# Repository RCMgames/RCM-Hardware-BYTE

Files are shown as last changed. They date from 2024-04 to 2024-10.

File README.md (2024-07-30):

# RCM-Hardware-BYTE
v2.3

* 1.25 by 1.25 inches, 31.75 by 31.75 millimeters
* 8 motors
* 8 servos
* battery monitoring
* I2C connector on QT PY
* runs on 3-11 volts

### Tested with the following types of ESP32 QT Py:
| Type of Qt Py | PlatformIO name | link to Adafruit |
| --- | --- | --- |
| S3 with 2MB PSRAM |  adafruit_qtpy_esp32s3_n4r2 |  https://www.adafruit.com/product/5700 |
| S3 with 8Mb Flash |  adafruit_qtpy_esp32s3_nopsram |  https://www.adafruit.com/product/5426 |
| S2 |  adafruit_qtpy_esp32s2 |  https://www.adafruit.com/product/5325  |

Look here for how to program it: https://github.com/RCMgames/RCMv2

Look here for more information and examples of robots: https://github.com/rcmgames

Want slightly smaller with a built in IMU? Look at the [Nibble](https://github.com/RCMgames/RCM-Hardware-Nibble)

## Options for purchasing

* [PCBWay link](https://www.pcbway.com/project/shareproject/RCMHardwareByte_v2_3_e23eec63.html) (PCBWay will give me a commission without increasing the price for you). (approximately $90 for 2 boards and manufacturing took a month).
* send the gerbers, bill of materials, and ComponentPlacement files to a PCB manufacturer of your choice (details you may be asked for: min hole 0.25mm, min track/spacing 5/5mil, thickness 1.0mm, 1 oz Cu outer 1.5 oz Cu inner)

## Components
Solder by hand to complete the assembly of your boards.
| part | links | quantity | notes |
| ----- | ----- | ----- | ----- |
| RCM BYTE circuit board | [options for purchasing](https://github.com/RCMgames/RCM-Hardware-BYTE/tree/main#options-for-purchasing) | 1 | |
| ESP32 QT Py | [compatible QT Py](https://github.com/RCMgames/RCM-Hardware-BYTE/tree/main#tested-with-the-following-types-of-esp32-qt-py) | 1 | |
| 2x8 female header pins | [this](https://www.digikey.com/en/products/detail/sullins-connector-solutions/PPPC042LFBN-RC/810244) or 2 strips of 8 | 1 | for motors |
| 7 female header pins | | 2 | for QT Py |
| 8 male header pins | | 4 | for servos |
| battery wires | JST RCY OR 9V battery snap | 1 | [Amazon JST RCY](https://www.amazon.com/dp/B00Z04QFN2/) |
| servo buck boost 5v 2A OR replace with a short length of wire| [Pololu](https://www.pololu.com/product/4085) | 2 | regulators are needed if you want to supply voltages above or below what servos can accept. There are 2 servo power buses, each with 4 servos. |

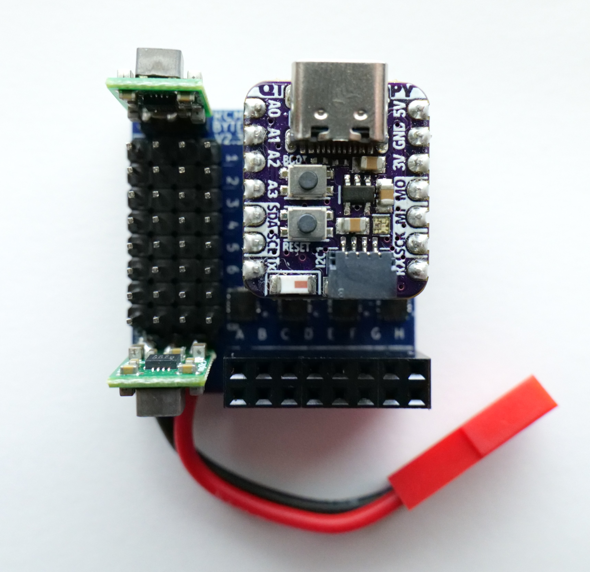
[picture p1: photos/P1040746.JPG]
front view

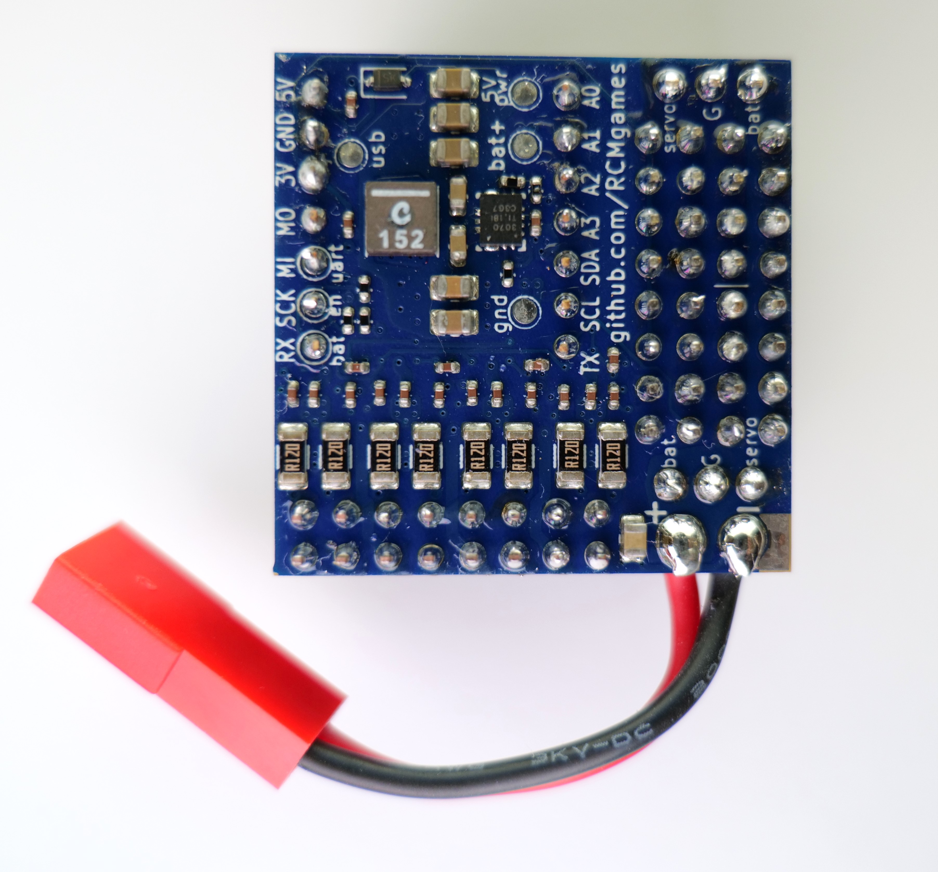
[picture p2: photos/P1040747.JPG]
back view


## Acknowledgements
* I would like to thank [PCBWay](https://www.pcbway.com/) for sponsoring prototyping runs of this project. PCBWay produces very nice boards, supports open source hardware, and gave me great support as I worked on this project. Special thanks to Liam!

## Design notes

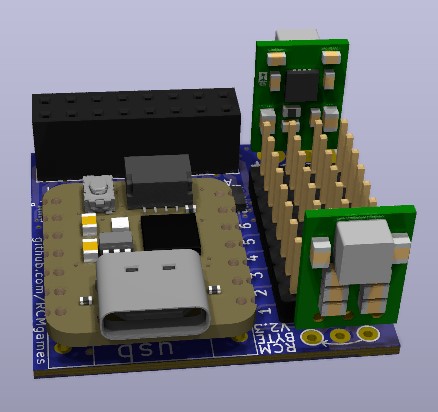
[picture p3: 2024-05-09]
CAD renders/render 1.jpg

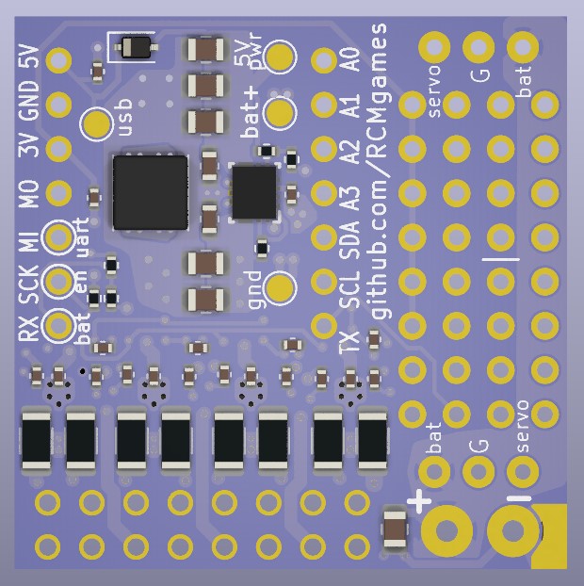
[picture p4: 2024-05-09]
CAD renders/back.jpg

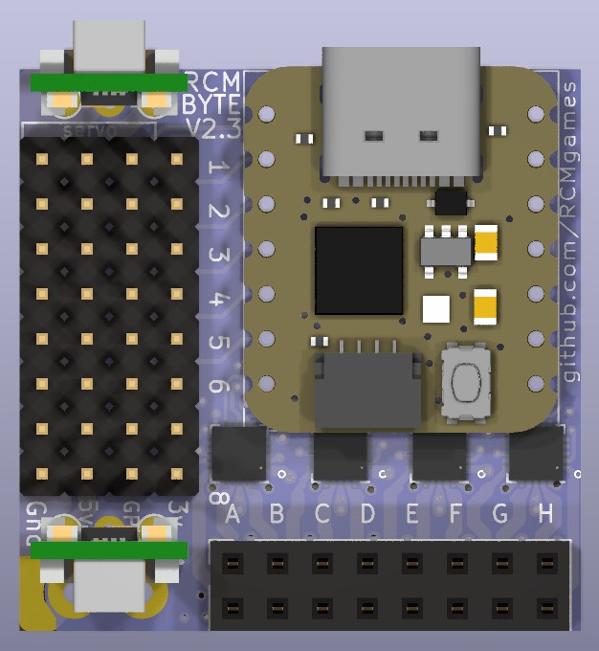
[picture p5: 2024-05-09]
CAD renders/top.jpg

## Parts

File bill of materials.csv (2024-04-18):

Reference | Value | Footprint | Datasheet | Manufacturer | Package | digikey part # | link | mount_type | mpn | Qty
C1, C3-C15, C17-C20, C22 | 100nF/0402/16V/X7R/<=10%/ceramic | Capacitor_SMD:C_0402_1005Metric | ~ | Cal-Chip Electronics, Inc. | 0402 | 4713-GMC04X7R104K50NTCT-ND | https://www.digikey.com/en/products/detail/cal-chip-electronics-inc/GMC04X7R104K50NT/18151122 | smt | GMC04X7R104K50NT | 19
C2, C25-C27 | 22uF/0805/>=16V | Capacitor_SMD:C_0805_2012Metric | ~ | Cal-Chip Electronics, Inc. | 0805 | 4713-GMC21X5R226M16NTCT-ND | https://www.digikey.com/en/products/detail/cal-chip-electronics-inc/GMC21X5R226M16NT/19910713 | smt | GMC21X5R226M16NT | 4
C16, C21 | 10uF/0805/>=16V | Capacitor_SMD:C_0805_2012Metric | ~ | Cal-Chip Electronics, Inc. | 0805 | 4713-GMC21X7R106K16NTCT-ND | https://www.digikey.com/en/products/detail/cal-chip-electronics-inc/GMC21X7R106K16NT/18151068 | smt | GMC21X7R106K16NT | 2
C23, C24 | 10uF/0603/>=16V | Capacitor_SMD:C_0603_1608Metric | ~ | Cal-Chip Electronics, Inc. | 0603 | 4713-GMC10X5R106M25NTCT-ND | https://www.digikey.com/en/products/detail/cal-chip-electronics-inc/GMC10X5R106M25NT/18151144 | smt | GMC10X5R106M25NT | 2
D1 | 1A Zener Diode / >=1A / 600 mV Vf @ 1 A | Diode_SMD:D_SOD-323 | ~ | Good-Ark Semiconductor | D_SOD-323 | 4786-GDB5818WSCT-ND | https://www.digikey.com/en/products/detail/good-ark-semiconductor/GDB5818WS/18648294 | smt | GDB5818WS | 1
ESP32_QT_PY1 | microcontroller | !RCMhardware footprints:ESP32 QT PY | ~ | Adafruit | tht |  | https://www.digikey.com/en/products/detail/adafruit-industries-llc/5426/21283802 | do not place or purchase for PCB assembly |  | 1
IC1-IC4 | TMC7300 | !RCMhardware footprints:QFN-20-1EP_3x3mm_P0.4mm_EP1.65x1.65mm | https://www.analog.com/media/en/technical-documentation/data-sheets/TMC7300_datasheet_rev1.08.pdf | Analog Devices | QFN-20-1EP_3x3mm_P0.4mm_EP1.65x1.65mm | 175-TMC7300-LA-TCT-ND | https://www.digikey.com/en/products/detail/analog-devices-inc-maxim-integrated/TMC7300-LA-T/11483537 | smt | TMC7300-LA-T | 4
J1 | pads to solder wires to, recommend JST RCY | !RCMhardware footprints:battery wires | ~ |  | tht |  | https://www.amazon.com/dp/B00Z04QFN2/ | do not place or purchase for PCB assembly |  | 1
J2-J5 | 1x08 male header pins | !RCMhardware footprints:servo pin column | ~ |  | tht |  | https://www.digikey.com/en/products/detail/te-connectivity-passive-product/CRG0402F30K/2390530 | do not place or purchase for PCB assembly |  | 4
J6 | 2x08 female header pins | !RCMhardware footprints:PinSocket_2x08_P2.54mm_Vertical | ~ |  | tht |  | https://www.digikey.com/en/products/detail/sullins-connector-solutions/PPTC082LFBN-RC/810214 | do not place or purchase for PCB assembly |  | 1
L1 | XFL4020-1.5μH | !RCMhardware footprints:L_Coilcraft_XxL4020 | ~ | Coilcraft | 1616 | 2457-XFL4020-152MEC-ND | https://www.digikey.com/en/products/detail/coilcraft/XFL4020-152MEC/21381168 | smt | XFL4020-152MEC | 1
R1, R14 | 30k / <=1% | Resistor_SMD:R_0402_1005Metric | ~ | TE Connectivity Passive Product | 0402 | 1712-CRG0402F30KCT-ND | https://www.digikey.com/en/products/detail/te-connectivity-passive-product/CRG0402F30K/2390530 | smt | CRG0402F30K | 2
R2, R11, R12 | 10k / <=1% | Resistor_SMD:R_0402_1005Metric | ~ | TE Connectivity Passive Product | 0402 | A121528CT-ND | https://www.digikey.com/en/products/detail/te-connectivity-passive-product/CRG0402F10K/5246515 | smt | CRG0402F10K | 3
R3-R10 | 120mΩ / 0.5W / 1206 / <=1% | Resistor_SMD:R_1206_3216Metric | ~ | Bourns Inc. | 1206 | CRL1206-FW-R120ELFCT-ND | https://www.digikey.com/en/products/detail/bourns-inc/CRL1206-FW-R150ELF/3785721 | smt | CRL1206-FW-R120ELF | 8
R13 | 130k | Resistor_SMD:R_0402_1005Metric | ~ | TE Connectivity Passive Product | 0402 | A119923CT-ND | https://www.digikey.com/en/products/detail/te-connectivity-passive-product/CPF0402B130KE/4966473 | smt | CPF0402B130KE | 1
TP1-TP4 | TestPoint | TestPoint:TestPoint_Pad_D1.5mm | ~ | n/a | n/a | n/a | n/a | do not place or purchase for PCB assembly | n/a | 4
U1 | TPS63070 5V 2A buck-boost | !RCMhardware footprints:TPS630701RNMR | https://www.ti.com/lit/ds/symlink/tps63070.pdf | Texas Instruments | 15-VQFN-HR (3x2.5) | 296-44874-1-ND | https://www.digikey.com/en/products/detail/texas-instruments/TPS63070RNMR/6175216 | smt | TPS63070RNMR | 1
U5, U6 | 5V, 2A, buck boost | !RCMhardware footprints:pololu4085 | ~ | Pololu | tht |  | https://www.pololu.com/product/4085 | do not place or purchase for PCB assembly |  | 2

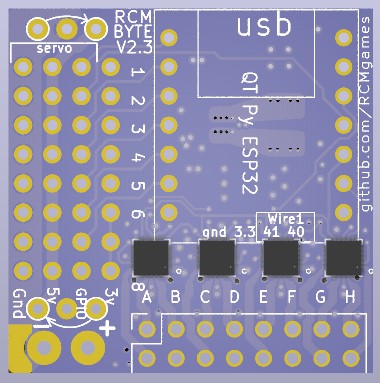
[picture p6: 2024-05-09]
CAD renders/top no components.jpg

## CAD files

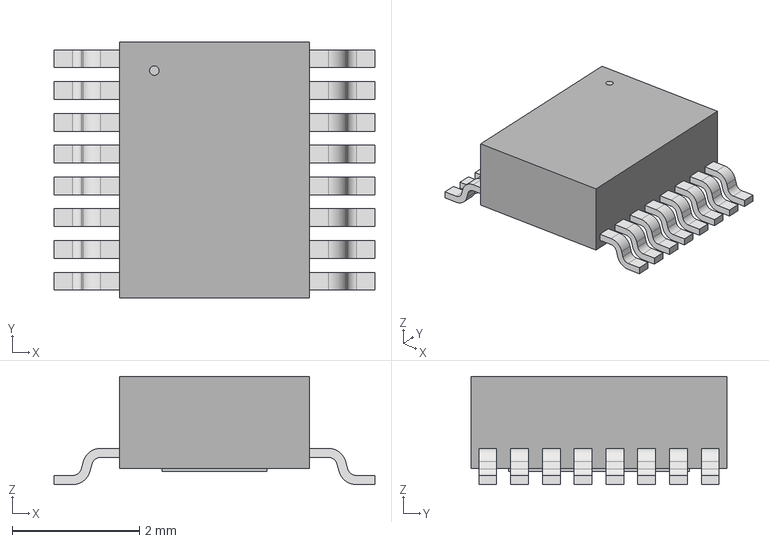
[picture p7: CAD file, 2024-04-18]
KiCad/!RCMhardware footprints/MSE_16_ADI.step
5.05 x 4.04 x 1.70 mm

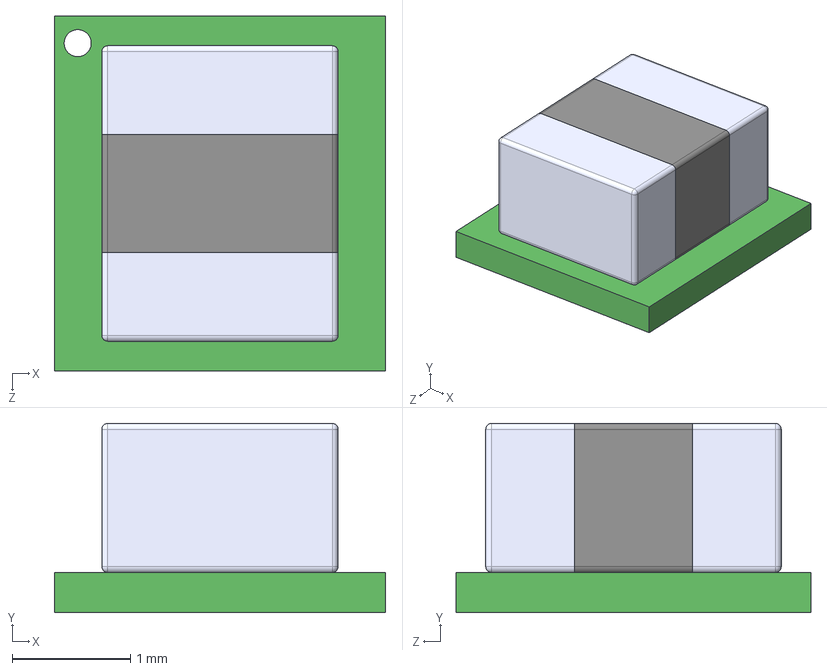
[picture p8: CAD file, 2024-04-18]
KiCad/!RCMhardware footprints/TPSM82903SISR--3DModel-STEP-56544.STEP
2.80 x 1.60 x 3.00 mm

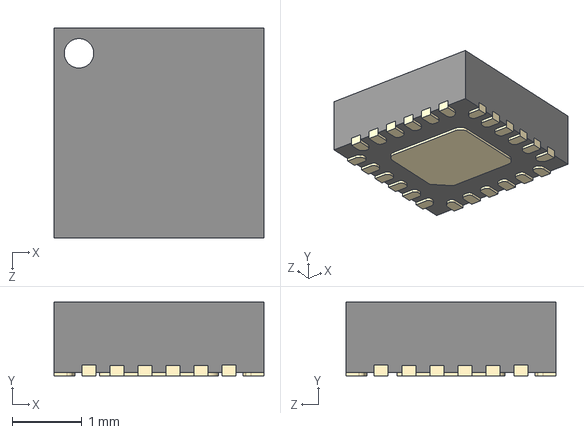
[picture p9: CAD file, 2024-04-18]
KiCad/!RCMhardware footprints/ICM-20948.step
3.00 x 1.05 x 3.00 mm

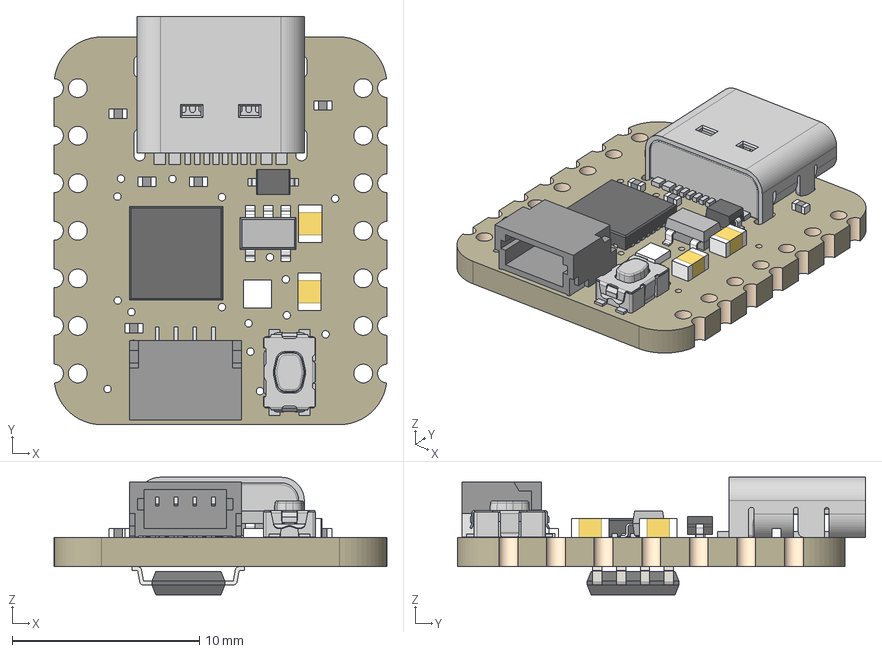
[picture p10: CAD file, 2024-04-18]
KiCad/!RCMhardware footprints/4600 QTPy.step
17.8 x 21.8 x 6.28 mm
Board
10uF x 2
reset
ATSAMD21E
TPB1,27
5.1K x 5
USB TYPE C
STEMMA_I2C_QTSKINNY
AP2112K-3.3
WS2812B_SK6805_1515
NSR0320
SOIC8_150MIL

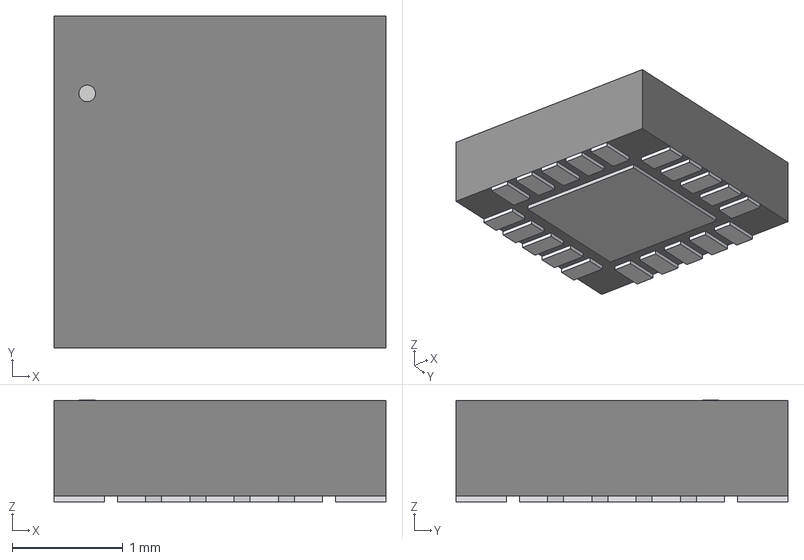
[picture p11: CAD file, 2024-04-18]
KiCad/!RCMhardware footprints/QFN20_3x3_TRI.step
3.00 x 3.00 x 0.917 mm

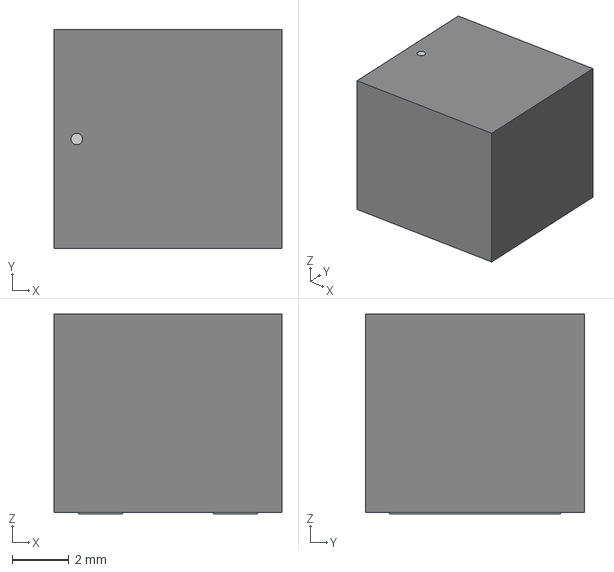
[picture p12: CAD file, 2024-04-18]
KiCad/!RCMhardware footprints/IND_XAL7070_COC.step
8.00 x 7.70 x 7.01 mm

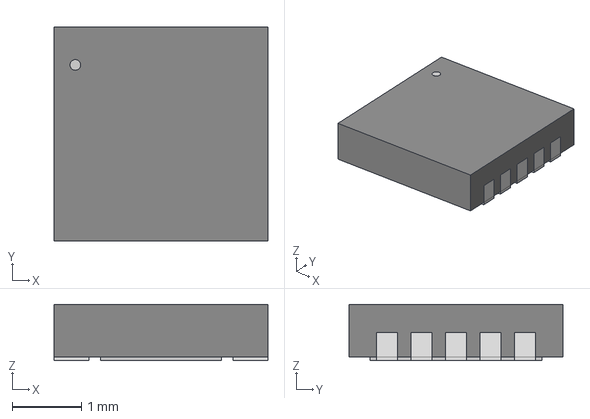
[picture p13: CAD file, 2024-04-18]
KiCad/!RCMhardware footprints/DFN-10_DD_LIT.step
3.10 x 3.10 x 0.815 mm

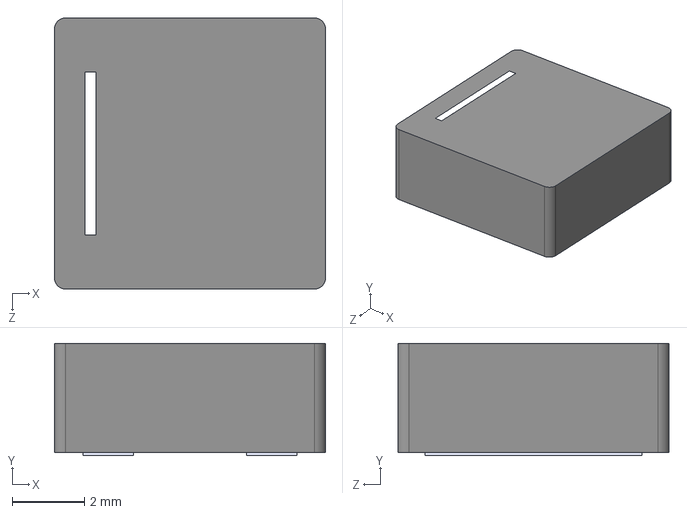
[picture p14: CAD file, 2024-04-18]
KiCad/!RCMhardware footprints/XAL7030-472MEC.step
7.50 x 3.10 x 7.50 mm

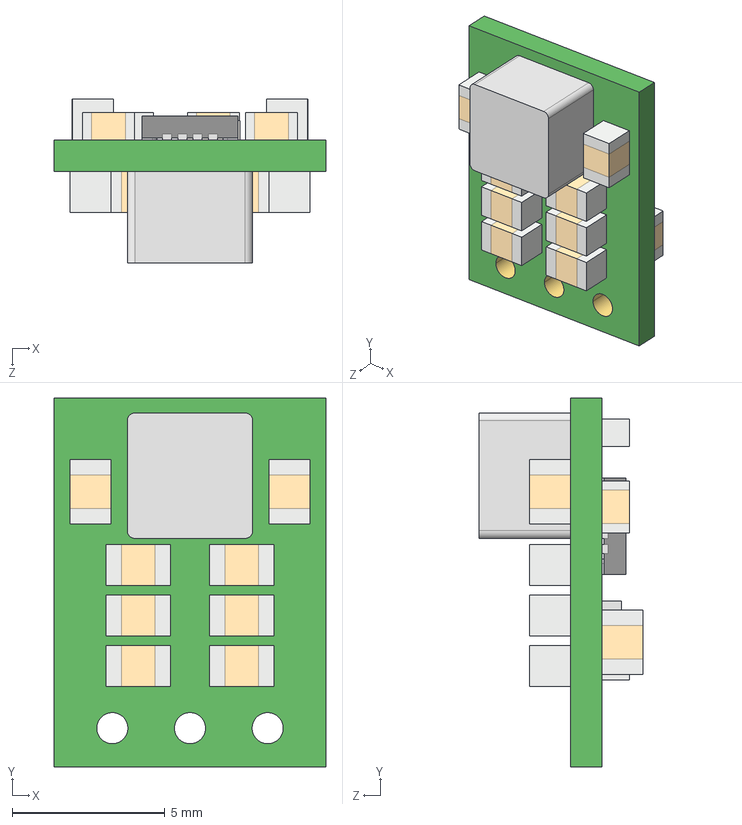
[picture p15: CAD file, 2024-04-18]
KiCad/!RCMhardware footprints/pololu 4085 5v-2a-step-up-step-down-voltage-regulator-s13v20f5.step
8.89 x 12.1 x 5.37 mm

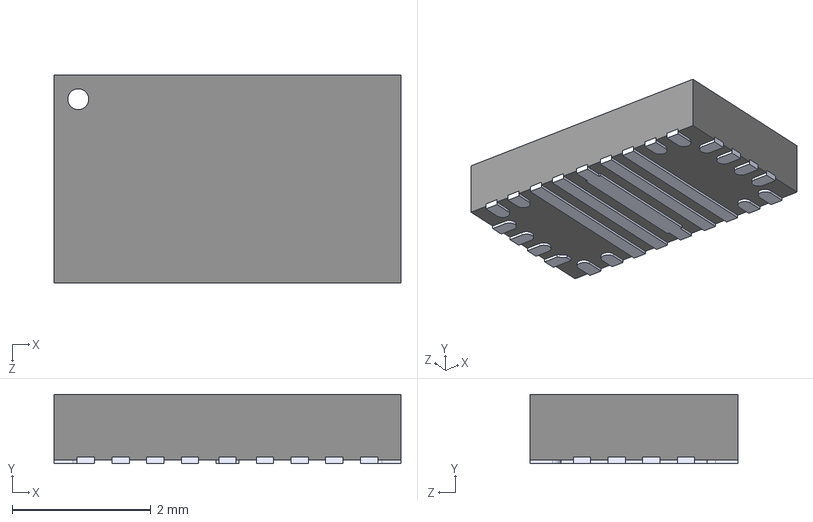
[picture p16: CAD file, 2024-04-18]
KiCad/!RCMhardware footprints/TPS552892RYQR.step
5.00 x 1.00 x 3.00 mm

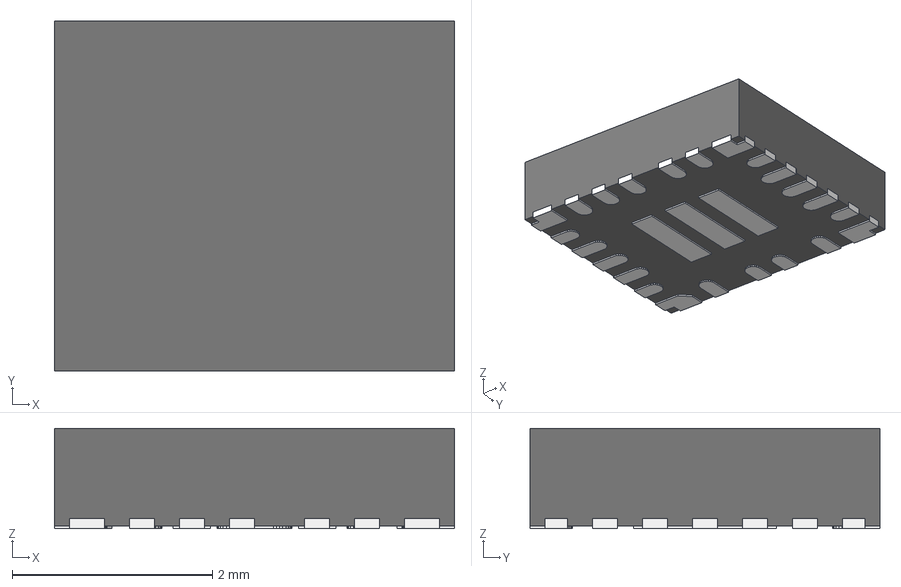
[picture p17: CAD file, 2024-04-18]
KiCad/!RCMhardware footprints/TPS552882RPMR.stp
4.00 x 3.50 x 1.00 mm
FRAME
MOLD

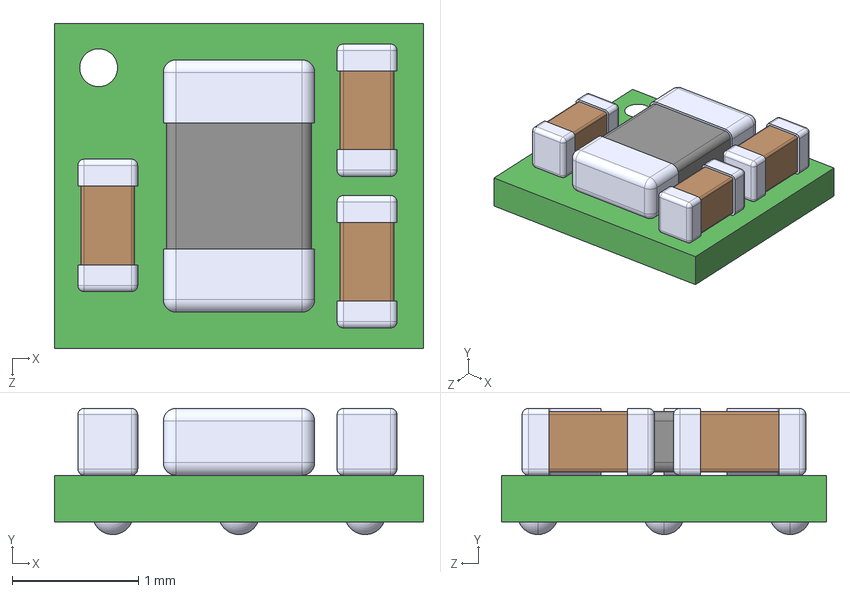
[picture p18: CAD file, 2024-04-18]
KiCad/!RCMhardware footprints/TPS81256SIPT--3DModel-STEP-56544.STEP
2.92 x 1.00 x 2.58 mm

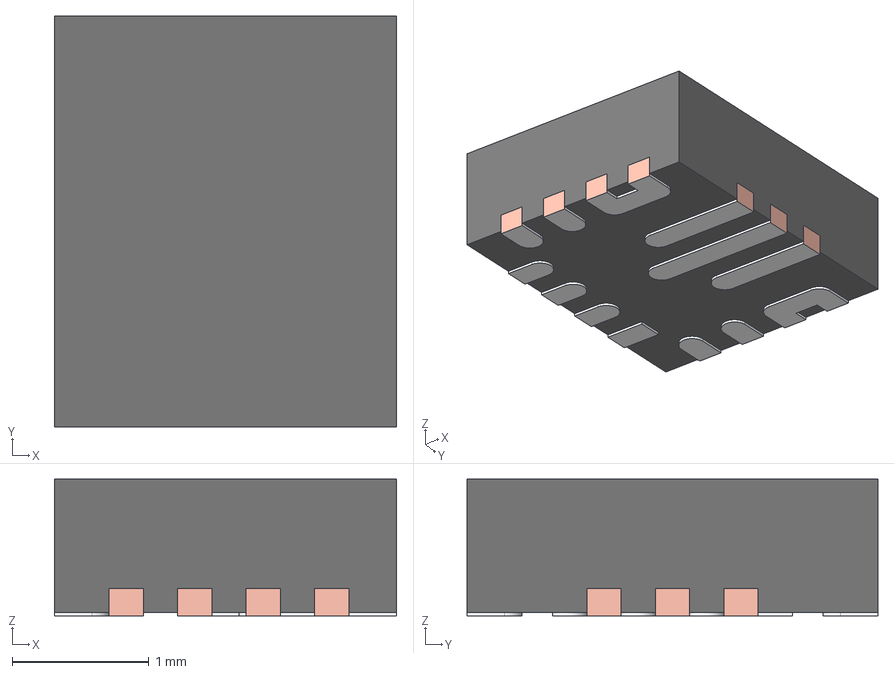
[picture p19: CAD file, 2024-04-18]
KiCad/!RCMhardware footprints/TPS630701RNMR.stp
2.50 x 3.00 x 1.00 mm
FRAME-RNM0015A
BODY-QFN
PIN1-ID

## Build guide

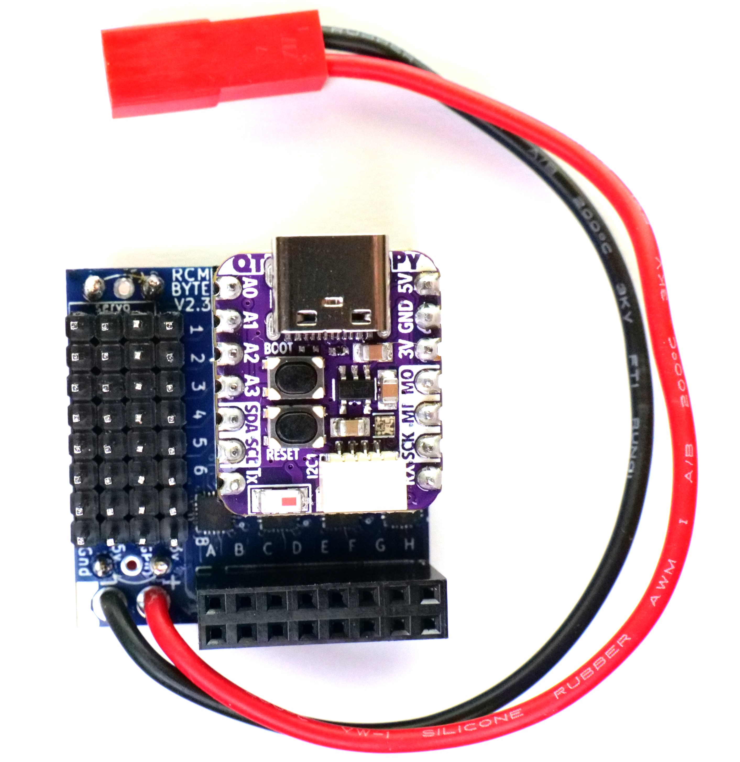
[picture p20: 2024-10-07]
photos/assembled byte without regulators top view - P1040805_2.JPG

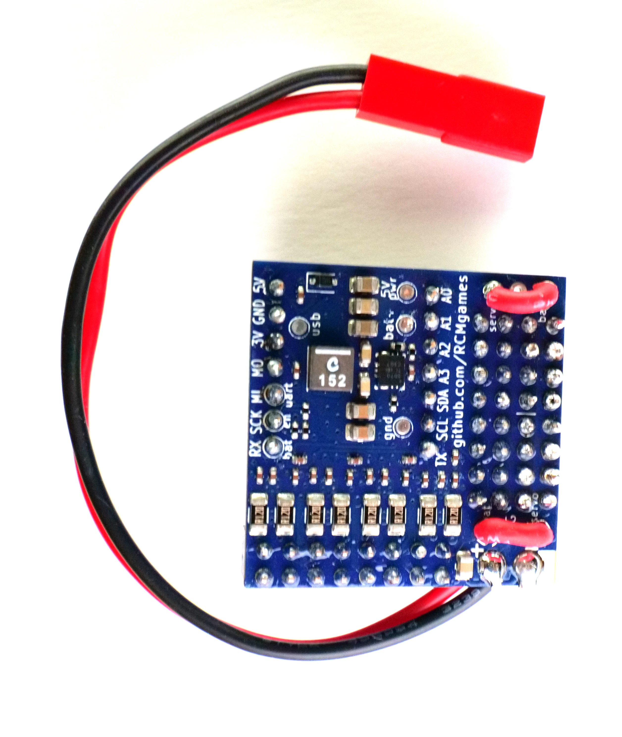
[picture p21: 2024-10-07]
photos/assembled byte without regulators bottom view - P1040806_2.JPG

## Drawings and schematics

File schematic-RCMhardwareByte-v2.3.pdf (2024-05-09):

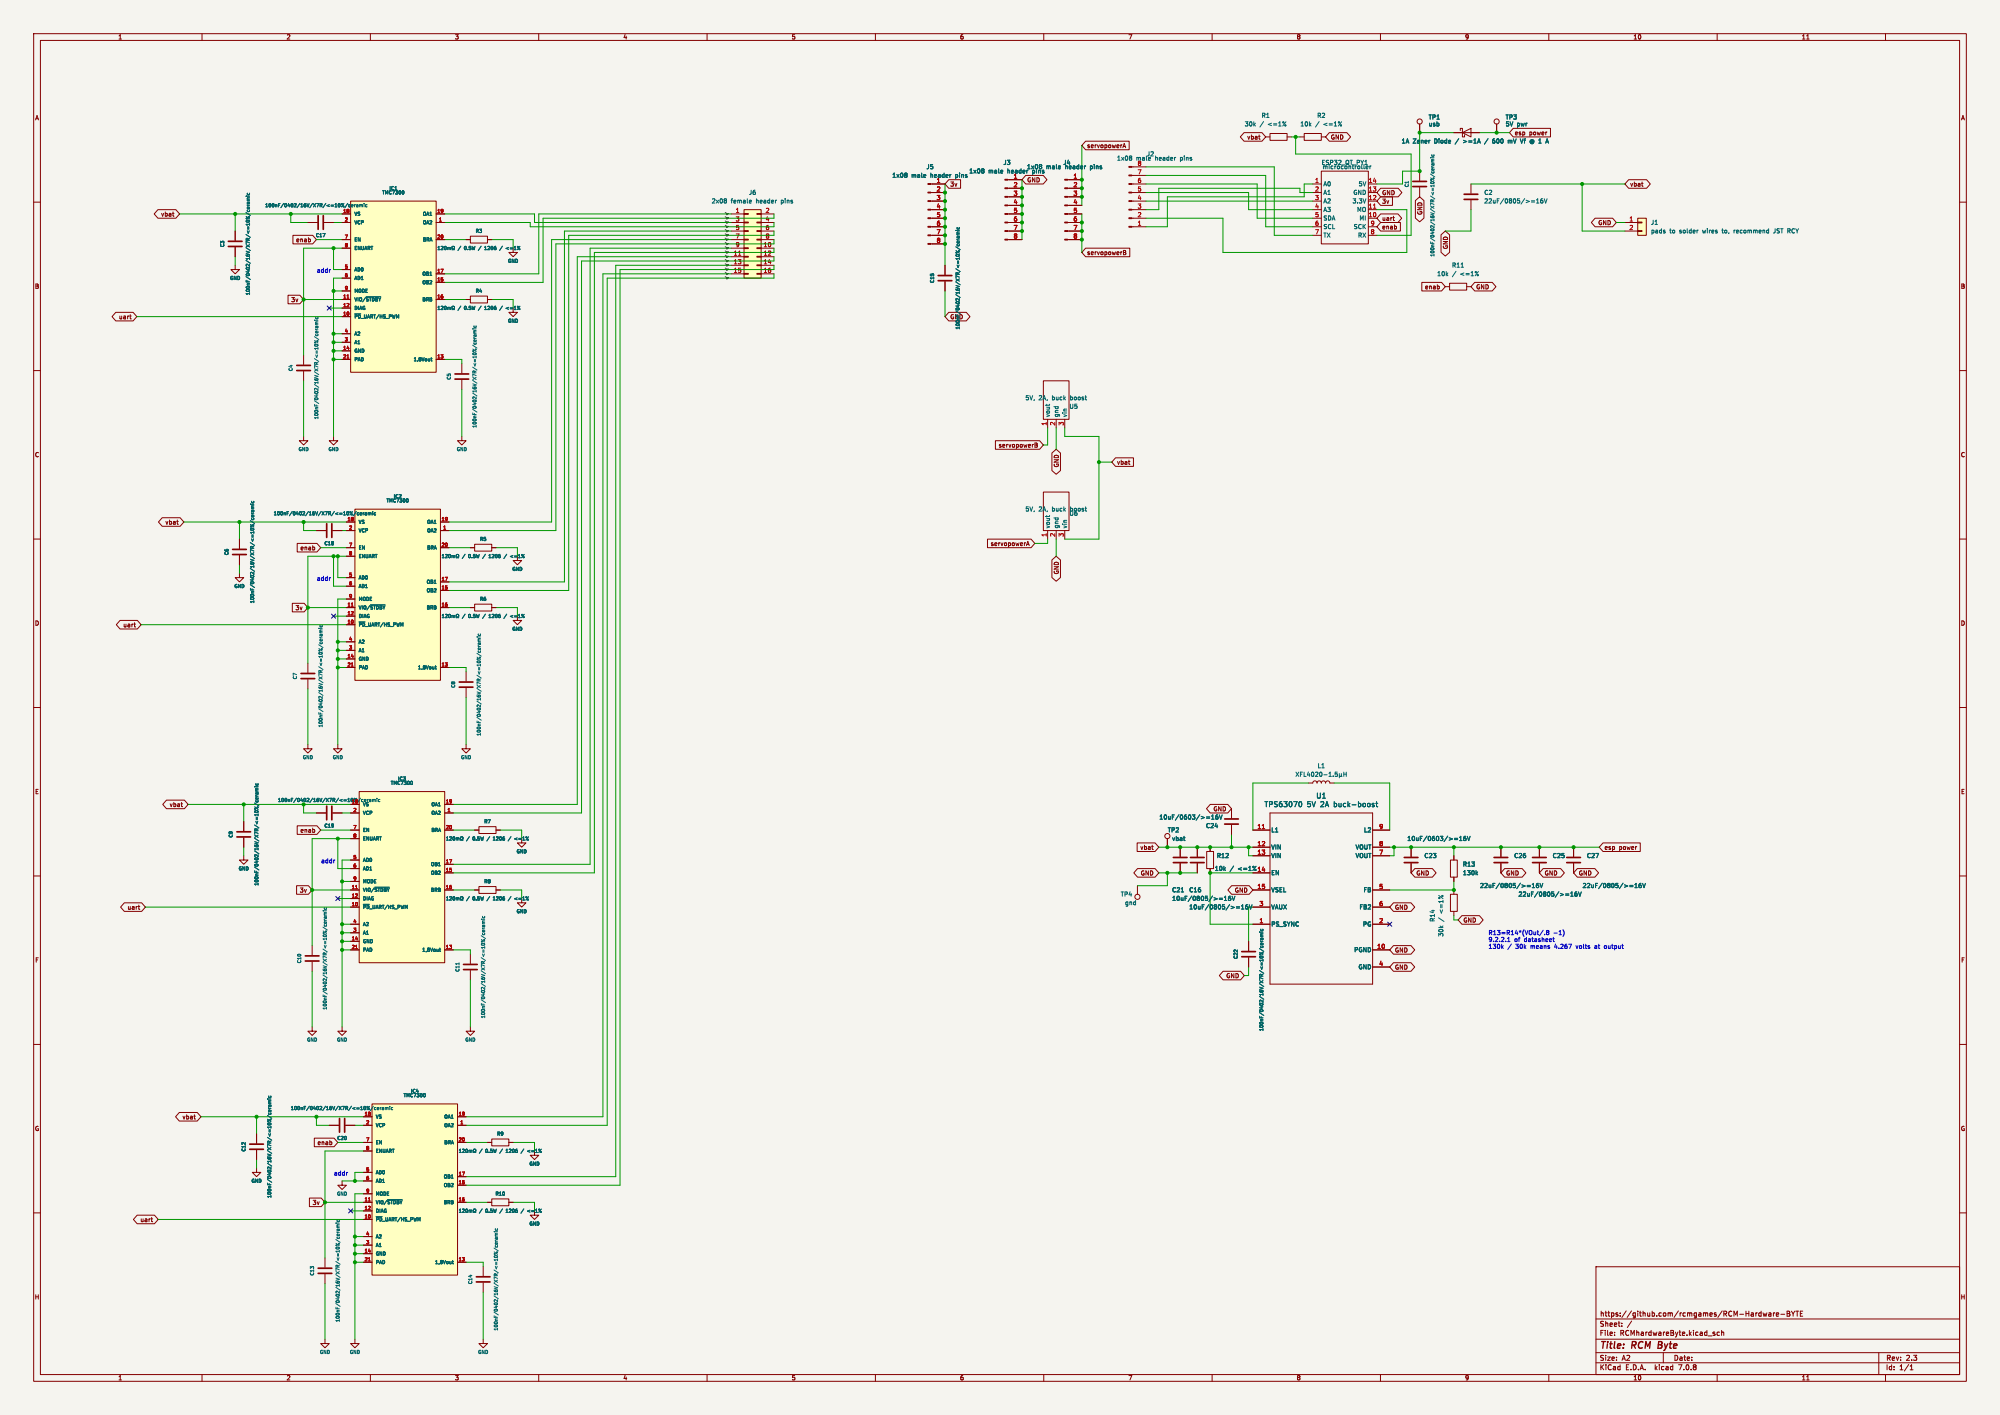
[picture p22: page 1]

1A Zener Diode / >=1A / 600 mV Vf @ 1 A

File: RCMhardwareByte.kicad_sch Sheet: / https://github.com/rcmgames/RCM-Hardware-BYTE

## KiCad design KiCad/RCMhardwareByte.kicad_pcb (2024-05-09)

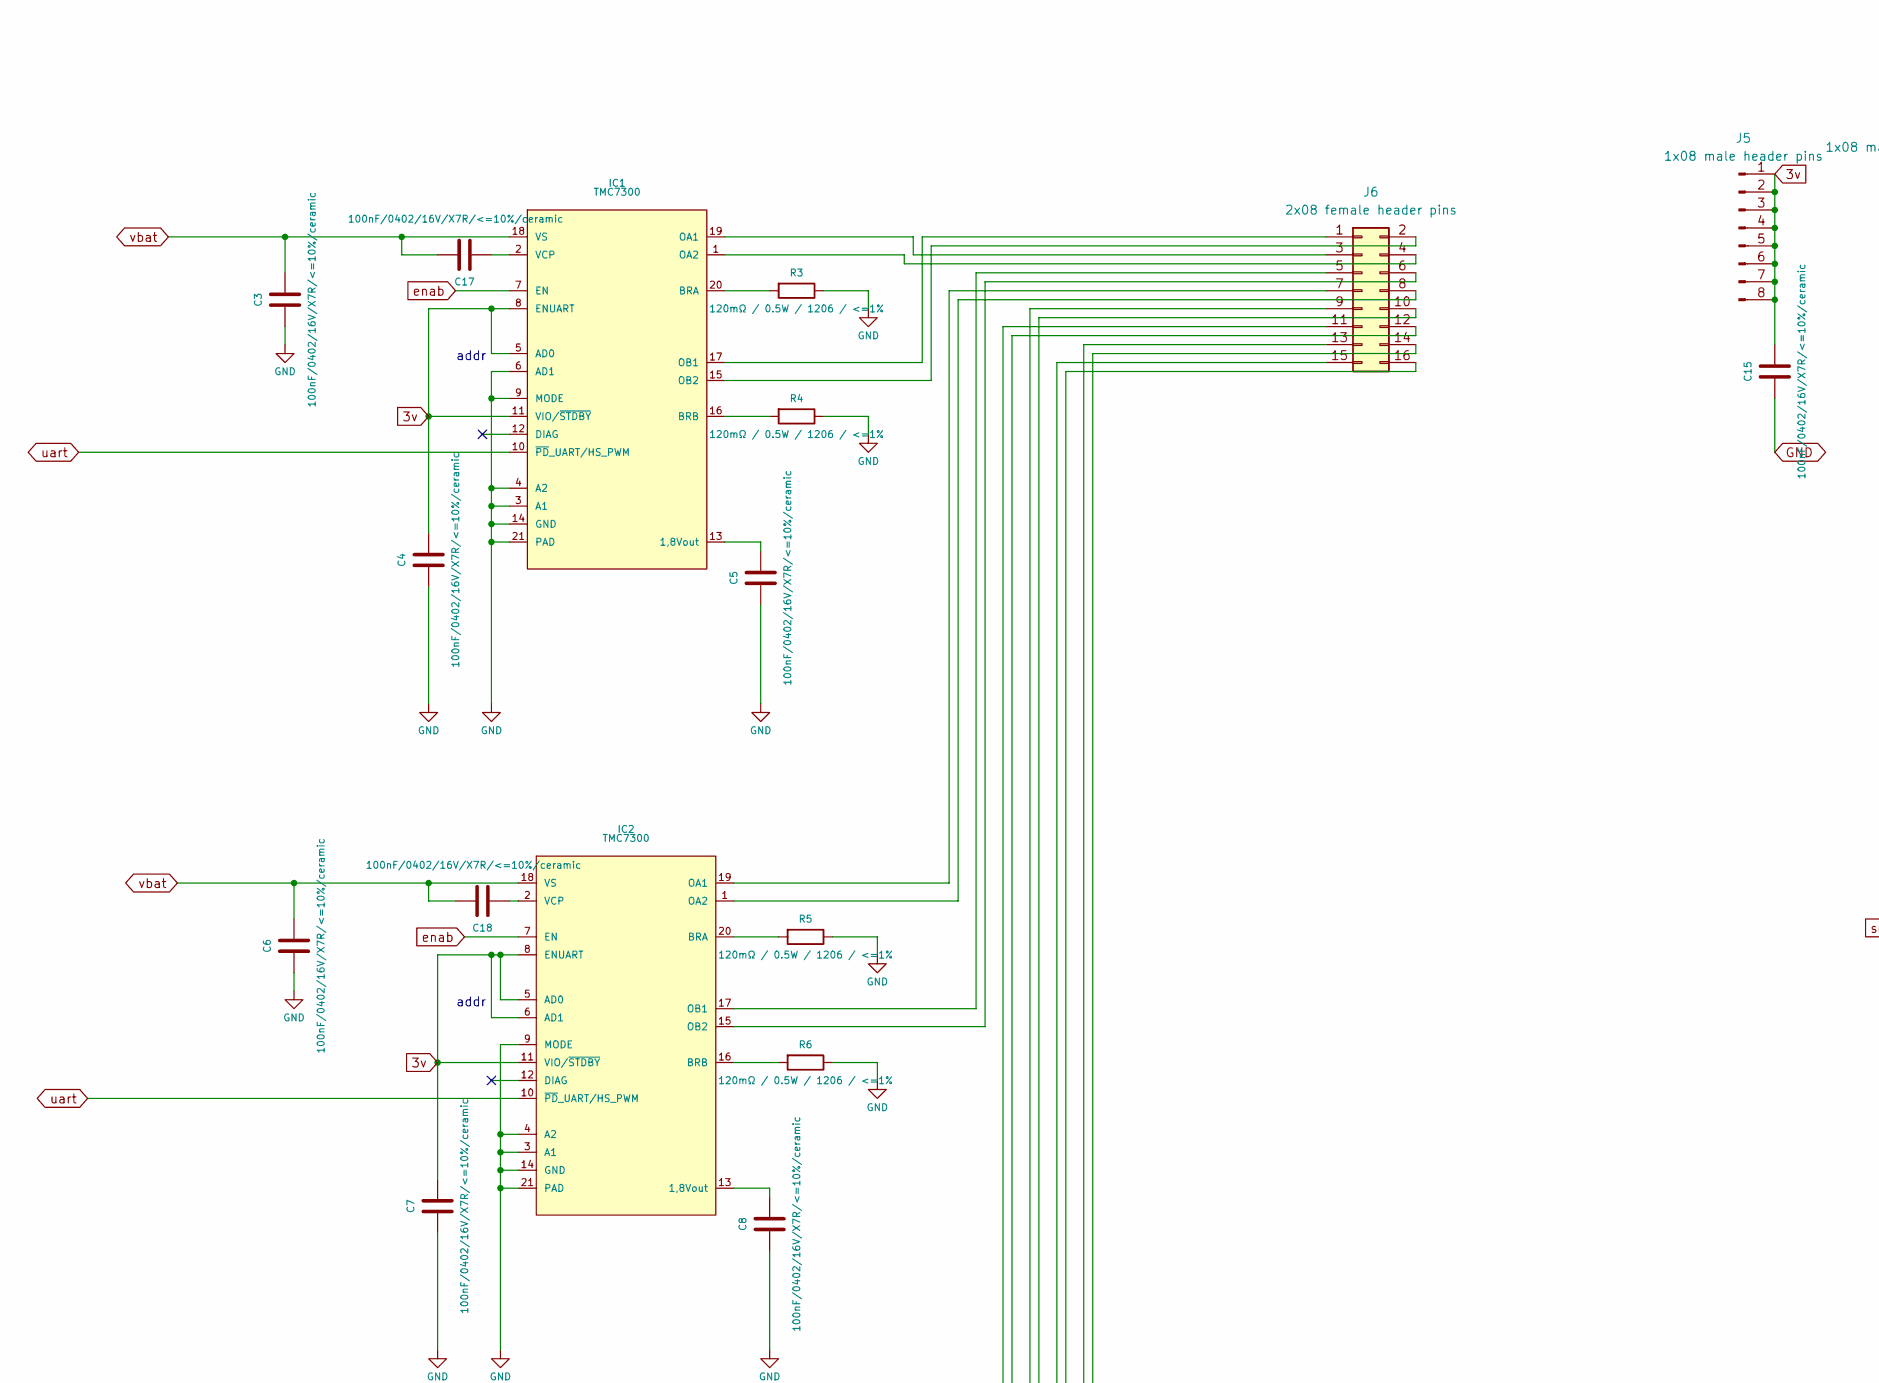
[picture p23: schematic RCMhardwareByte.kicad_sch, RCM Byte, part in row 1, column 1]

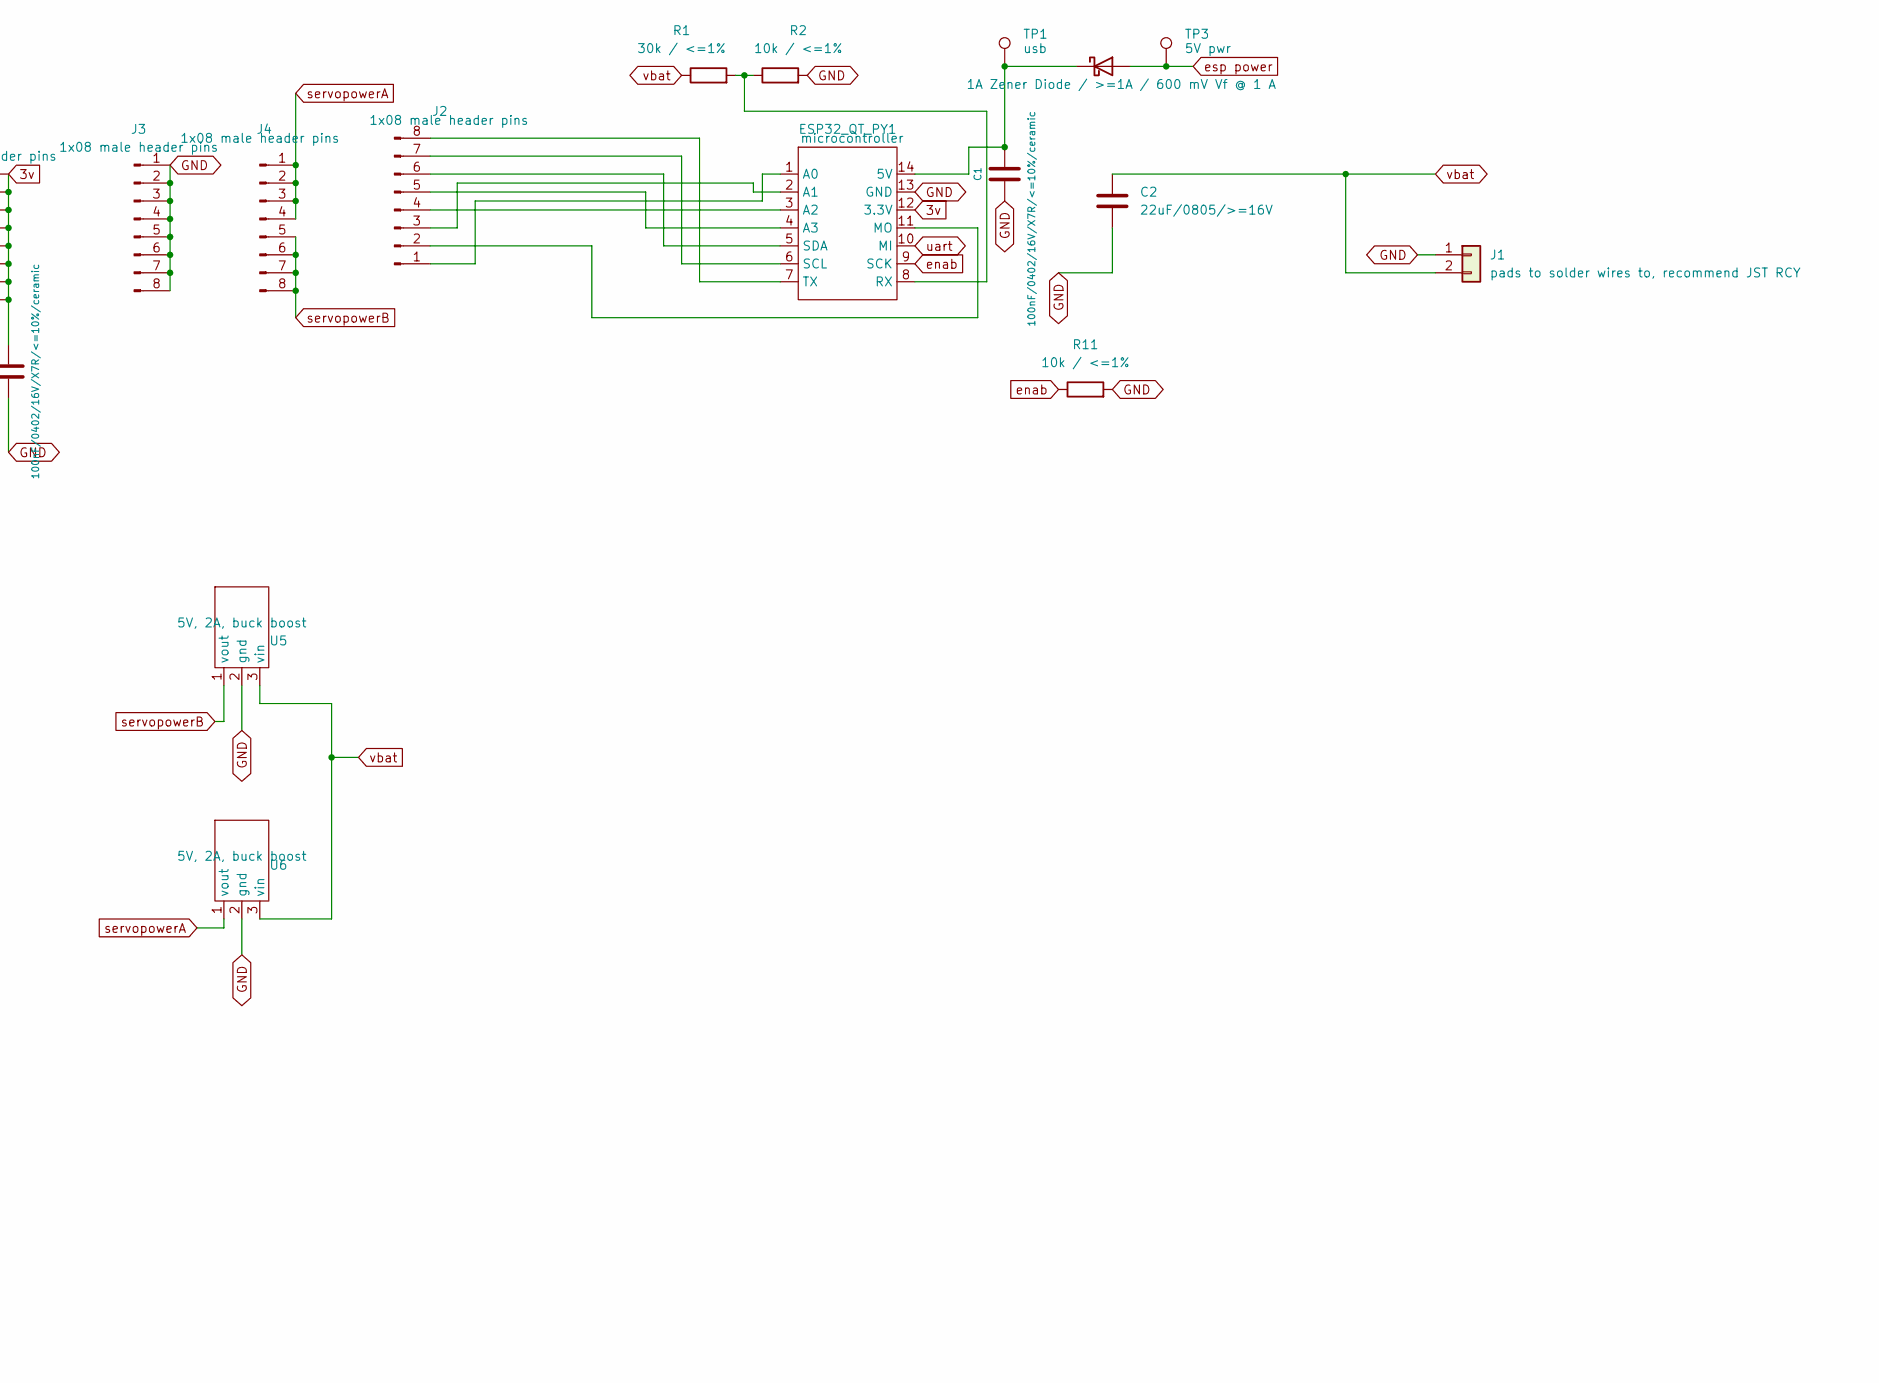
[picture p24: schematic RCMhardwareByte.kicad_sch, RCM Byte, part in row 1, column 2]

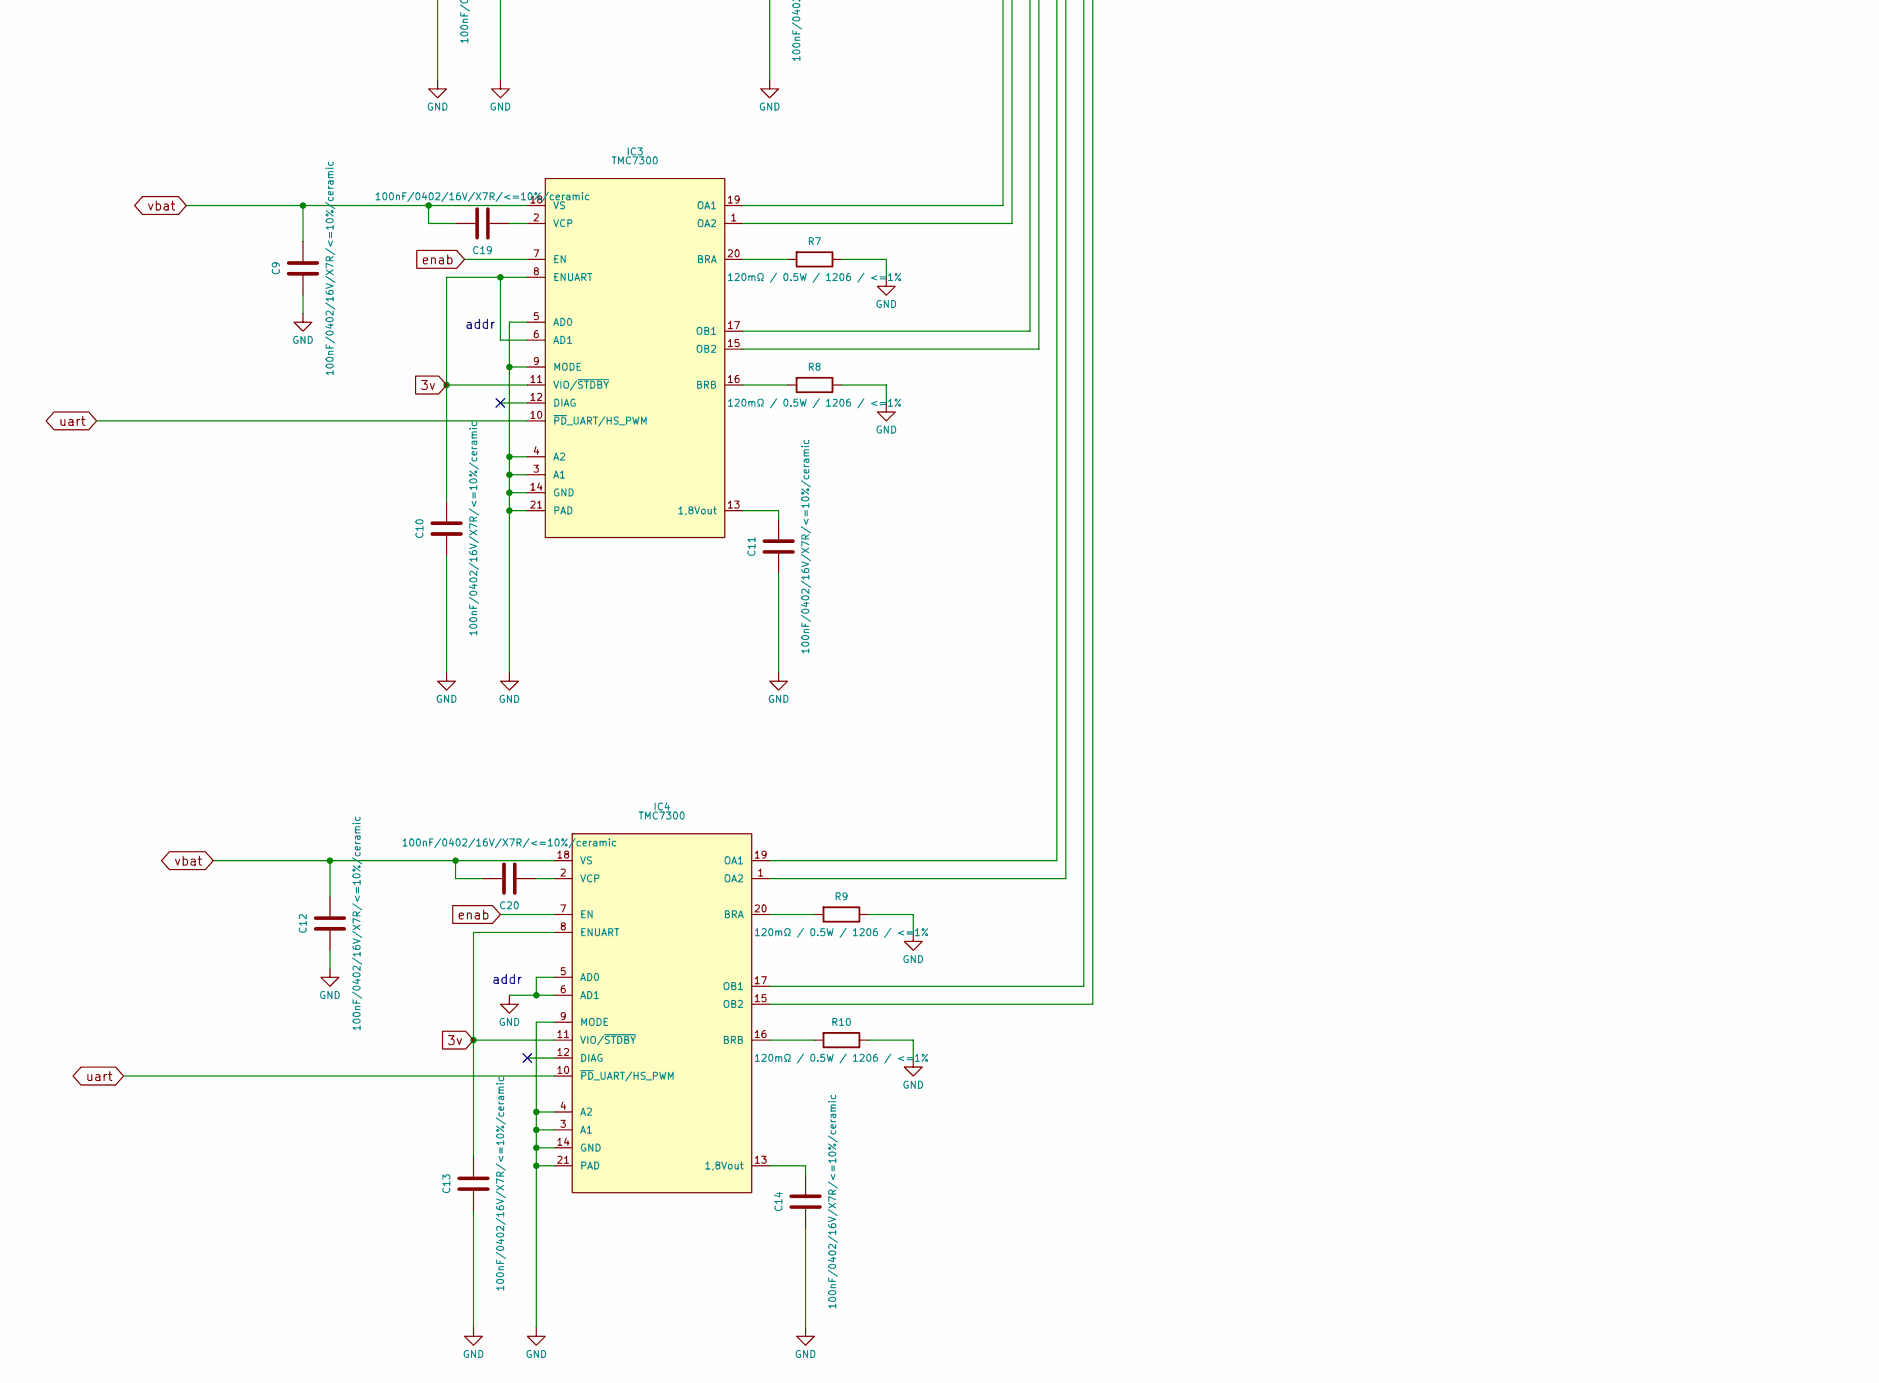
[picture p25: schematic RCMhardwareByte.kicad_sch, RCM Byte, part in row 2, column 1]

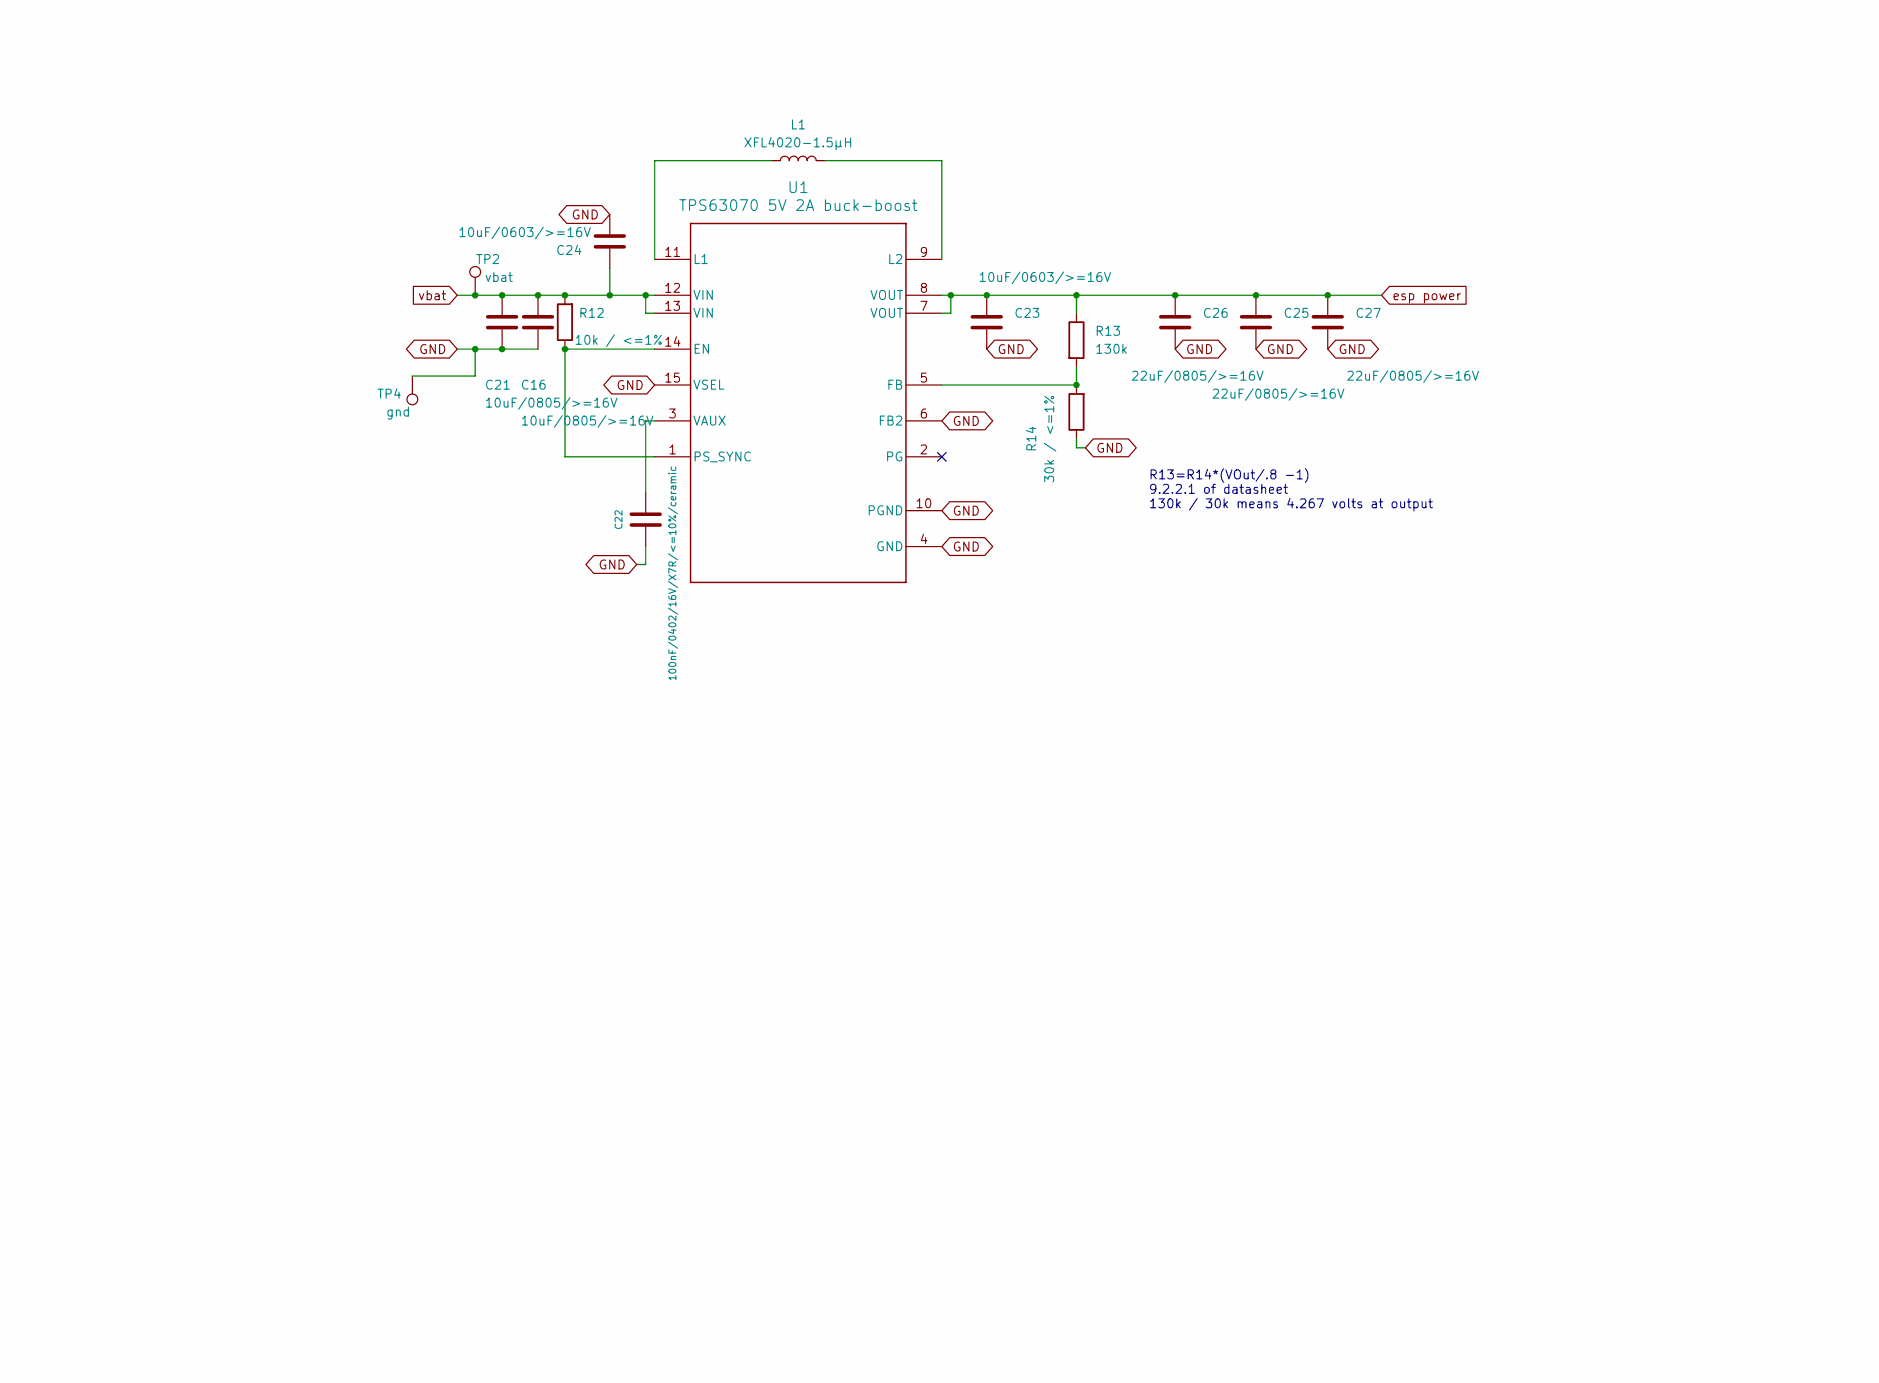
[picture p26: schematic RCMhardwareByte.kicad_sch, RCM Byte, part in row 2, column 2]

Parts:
C1, C3, C4, C5, C6, C7, C8, C9, C10, C11, C12, C13, C14, C15, C17, C18, C19, C20, C22: 100nF/0402/16V/X7R/<=10%/ceramic; C_0402_1005Metric; mpn GMC04X7R104K50NT; digikey part # 4713-GMC04X7R104K50NTCT-ND
C2, C25, C26, C27: 22uF/0805/>=16V; C_0805_2012Metric; mpn GMC21X5R226M16NT; digikey part # 4713-GMC21X5R226M16NTCT-ND
C16, C21: 10uF/0805/>=16V; C_0805_2012Metric; mpn GMC21X7R106K16NT; digikey part # 4713-GMC21X7R106K16NTCT-ND
C23, C24: 10uF/0603/>=16V; C_0603_1608Metric; mpn GMC10X5R106M25NT; digikey part # 4713-GMC10X5R106M25NTCT-ND
D1: 1A Zener Diode / >=1A / 600 mV Vf @ 1 A; D_SOD-323; mpn GDB5818WS; digikey part # 4786-GDB5818WSCT-ND
ESP32_QT_PY1: microcontroller; ESP32 QT PY
IC1, IC2, IC3, IC4: TMC7300; QFN-20-1EP_3x3mm_P0.4mm_EP1.65x1.65mm; mpn TMC7300-LA-T; digikey part # 175-TMC7300-LA-TCT-ND
J1: pads to solder wires to, recommend JST RCY; battery wires
J2, J3, J4, J5: 1x08 male header pins; servo pin column
J6: 2x08 female header pins; PinSocket_2x08_P2.54mm_Vertical
L1: XFL4020-1.5μH; L_Coilcraft_XxL4020; mpn XFL4020-152MEC; digikey part # 2457-XFL4020-152MEC-ND
R1, R14: 30k / <=1%; R_0402_1005Metric; mpn CRG0402F30K; digikey part # 1712-CRG0402F30KCT-ND
R2, R11, R12: 10k / <=1%; R_0402_1005Metric; mpn CRG0402F10K; digikey part # A121528CT-ND
R3, R4, R5, R6, R7, R8, R9, R10: 120mΩ / 0.5W / 1206 / <=1%; R_1206_3216Metric; mpn CRL1206-FW-R120ELF; digikey part # CRL1206-FW-R120ELFCT-ND
R13: 130k; R_0402_1005Metric; mpn CPF0402B130KE; digikey part # A119923CT-ND
TP1: usb; TestPoint_Pad_D1.5mm; mpn n/a; digikey part # n/a
TP2: vbat; TestPoint_Pad_D1.5mm; mpn n/a; digikey part # n/a
TP3: 5V pwr; TestPoint_Pad_D1.5mm; mpn n/a; digikey part # n/a
TP4: gnd; TestPoint_Pad_D1.5mm; mpn n/a; digikey part # n/a
U1: TPS63070 5V 2A buck-boost; TPS630701RNMR; mpn TPS63070RNMR; digikey part # 296-44874-1-ND
U5, U6: 5V, 2A, buck boost; pololu4085

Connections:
3v: C4.1, C7.1, C10.1, C13.1, C15.1, ESP32_QT_PY1.12 (3.3V), IC1.5 (AD0), IC1.8 (ENUART), IC1.11 (VIO/~STDBY), IC2.5 (AD0), IC2.6 (AD1), IC2.8 (ENUART), IC2.11 (VIO/~STDBY), IC3.6 (AD1), IC3.8 (ENUART), IC3.11 (VIO/~STDBY), IC4.8 (ENUART), IC4.11 (VIO/~STDBY), J5.1, J5.2, J5.3, J5.4, J5.5, J5.6, J5.7, J5.8
GND: C1.2, C2.2, C3.2, C4.2, C5.2, C6.2, C7.2, C8.2, C9.2, C10.2, C11.2, C12.2, C13.2, C14.2, C15.2, C16.2, C21.2, C22.2, C23.2, C24.2, C25.2, C26.2, C27.2, ESP32_QT_PY1.13 (GND), IC1.3 (A1), IC1.4 (A2), IC1.6 (AD1), IC1.9 (MODE), IC1.14 (GND), IC1.21 (PAD), IC2.3 (A1), IC2.4 (A2), IC2.9 (MODE), IC2.14 (GND), IC2.21 (PAD), IC3.3 (A1), IC3.4 (A2), IC3.5 (AD0), IC3.9 (MODE), IC3.14 (GND), IC3.21 (PAD), IC4.3 (A1), IC4.4 (A2), IC4.5 (AD0), IC4.6 (AD1), IC4.9 (MODE), IC4.14 (GND), IC4.21 (PAD), J1.1, J3.1, J3.2, J3.3, J3.4, J3.5, J3.6, J3.7, J3.8, R2.2, R3.1, R4.1, R5.1, R6.1, R7.1, R8.1, R9.1, R10.1, R11.2, R14.1, TP4.1, U1.4 (GND), U1.6 (FB2), U1.10 (PGND), U1.15 (VSEL), U5.2 (gnd), U6.2 (gnd)
unnamed: C1.1, D1.1 (K), ESP32_QT_PY1.14 (5V), TP1.1
unnamed: ESP32_QT_PY1.1 (A0), J2.1
unnamed: ESP32_QT_PY1.2 (A1), J2.3
unnamed: ESP32_QT_PY1.3 (A2), J2.4
unnamed: ESP32_QT_PY1.4 (A3), J2.5
unnamed: ESP32_QT_PY1.11 (MO), J2.2
unnamed: ESP32_QT_PY1.8 (RX), R1.2, R2.1
unnamed: ESP32_QT_PY1.6 (SCL), J2.7
unnamed: ESP32_QT_PY1.5 (SDA), J2.6
unnamed: ESP32_QT_PY1.7 (TX), J2.8
unnamed: C5.1, IC1.13 (1,8Vout)
unnamed: IC1.20 (BRA), R3.2
unnamed: IC1.16 (BRB), R4.2
unnamed: IC1.19 (OA1), J6.3
unnamed: IC1.1 (OA2), J6.4
unnamed: IC1.17 (OB1), J6.1
unnamed: IC1.15 (OB2), J6.2
unnamed: C17.2, IC1.2 (VCP)
unnamed: C8.1, IC2.13 (1,8Vout)
unnamed: IC2.20 (BRA), R5.2
unnamed: IC2.16 (BRB), R6.2
unnamed: IC2.19 (OA1), J6.7
unnamed: IC2.1 (OA2), J6.8
unnamed: IC2.17 (OB1), J6.5
unnamed: IC2.15 (OB2), J6.6
unnamed: C18.2, IC2.2 (VCP)
unnamed: C11.1, IC3.13 (1,8Vout)
unnamed: IC3.20 (BRA), R7.2
unnamed: IC3.16 (BRB), R8.2
unnamed: IC3.19 (OA1), J6.11
unnamed: IC3.1 (OA2), J6.12
unnamed: IC3.17 (OB1), J6.9
unnamed: IC3.15 (OB2), J6.10
unnamed: C19.2, IC3.2 (VCP)
unnamed: C14.1, IC4.13 (1,8Vout)
unnamed: IC4.20 (BRA), R9.2
unnamed: IC4.16 (BRB), R10.2
unnamed: IC4.19 (OA1), J6.15
unnamed: IC4.1 (OA2), J6.16
unnamed: IC4.17 (OB1), J6.13
unnamed: IC4.15 (OB2), J6.14
unnamed: C20.2, IC4.2 (VCP)
unnamed: R12.1, U1.1 (PS_SYNC), U1.14 (EN)
unnamed: R13.2, R14.2, U1.5 (FB)
unnamed: L1.1, U1.11 (L1)
unnamed: L1.2, U1.9 (L2)
unnamed: C22.1, U1.3 (VAUX)
enab: ESP32_QT_PY1.9 (SCK), IC1.7 (EN), IC2.7 (EN), IC3.7 (EN), IC4.7 (EN), R11.1
esp power: C23.1, C25.1, C26.1, C27.1, D1.2 (A), R13.1, TP3.1, U1.7 (VOUT), U1.8 (VOUT)
servopowerA: J4.1, J4.2, J4.3, J4.4, U6.1 (vout)
servopowerB: J4.5, J4.6, J4.7, J4.8, U5.1 (vout)
uart: ESP32_QT_PY1.10 (MI), IC1.10 (~PD_UART/HS_PWM), IC2.10 (~PD_UART/HS_PWM), IC3.10 (~PD_UART/HS_PWM), IC4.10 (~PD_UART/HS_PWM)
vbat: C2.1, C3.1, C6.1, C9.1, C12.1, C16.1, C17.1, C18.1, C19.1, C20.1, C21.1, C24.1, IC1.18 (VS), IC2.18 (VS), IC3.18 (VS), IC4.18 (VS), J1.2, R1.1, R12.2, TP2.1, U1.12 (VIN), U1.13 (VIN), U5.3 (vin), U6.3 (vin)

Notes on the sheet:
addr
R13=R14*(VOut/.8 -1) 9.2.2.1 of datasheet 130k / 30k means 4.267 volts at output

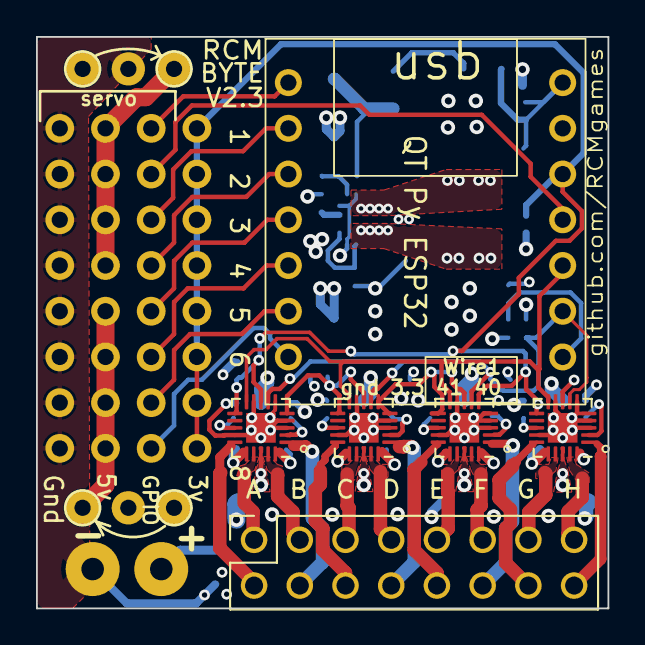
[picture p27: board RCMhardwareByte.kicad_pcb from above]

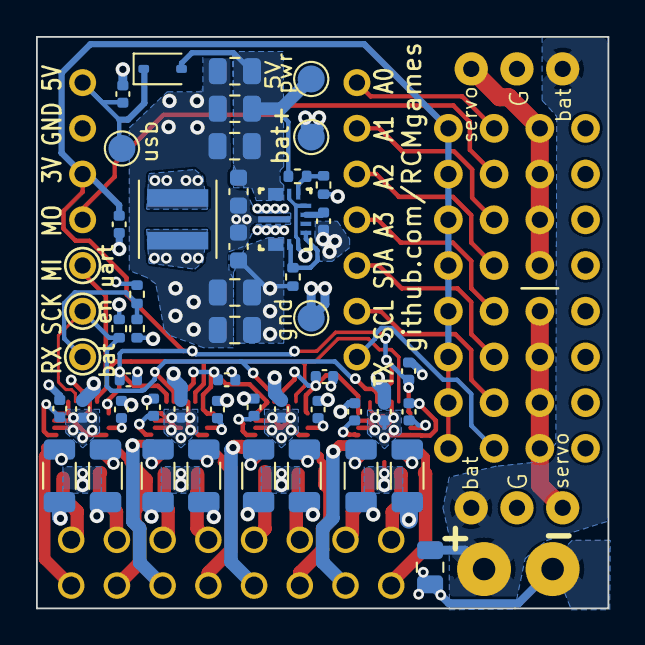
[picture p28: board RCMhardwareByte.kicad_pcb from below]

Board: 4 copper layers, 31.8 x 31.8 mm, 61 parts (48 on the bottom side), 55 nets.

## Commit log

2024-03-21 organize files
    [BOM.xlsx, T-I9W454600A-5sets-BOM(2023-11-15).xls]
2024-04-03 upload v2.1
    [BOM.xlsx, RCMhardwareByte.kicad_pcb, RCMhardwareByte.kicad_sch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]
2024-04-03 add 3d cad
2024-04-03 Create PCBWay Quote-5sets-RCMhardwareByteBOM(2024-04-03).xls
    [PCBWay Quote-5sets-RCMhardwareByteBOM(2024-04-03).xls]
2024-04-20 add pictures
    [T-I28W454600A-2sets-bill+of+materials(2024-04-19).xls]
